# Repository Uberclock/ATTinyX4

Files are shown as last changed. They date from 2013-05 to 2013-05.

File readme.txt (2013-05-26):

NancyHacker is based on Logxen's ATTinyX4 breakout and is designed to allow easy reconfiguration of a NancyDriver.

Basic Operation:

1) Plug a NancyDriver into the NancyHacker and use a MicroUSB cable to supply power to the NancyHacker.

2) The LED on the NancyHacker will flash to read out the set current on the driver board in amps. First it will count out slow flashes (1 second on, 1 second off) representing the integer then short flashes (0.5 second on, 0.5 second off) representing the tenths. So, a brand new NancyDriver should arrive set to 1.2A and so should read one long flash followed by two short flashes and a pause.

3) The UP and DOWN buttons can be used to adjust the set current by tenths. The NancyHacker will then read out the new setting over the LED. That's all there is to it. :)

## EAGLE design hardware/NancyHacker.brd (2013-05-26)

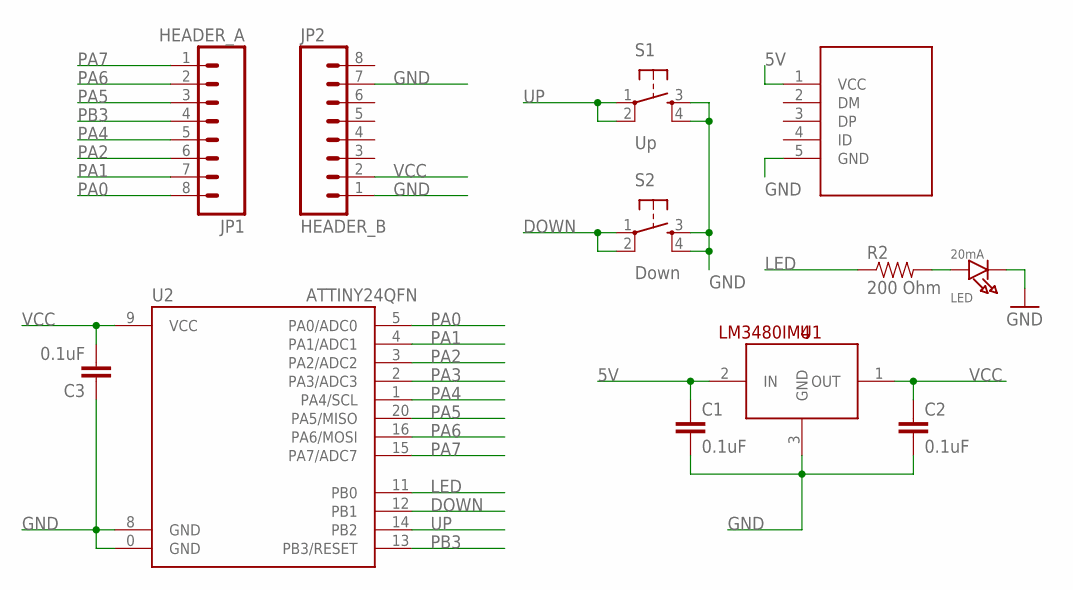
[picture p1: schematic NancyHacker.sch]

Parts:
C1, C2, C3: 0.1uF; 0603-CAP
JP1: HEADER_A; 1X08
JP2: HEADER_B; 1X08
LED: 20mA; CHIPLED_0603_NOOUTLINE
R2: 200 Ohm; 0402-RES
S1: Up; TACTILE_SWITCH_SMD
S2: Down; TACTILE_SWITCH_SMD
U1: LM3480IM4; SOT23-3
U2: ATTINY24QFN; QFN20
U$1: USB-MICROB-SMDRECEPT; USB-MICROB-RECEPT

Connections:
5V: C1.1, U1.2 (IN), U$1.1 (VCC)
DOWN: S2.1, S2.2, U2.12 (PB1)
GND: C1.2, C2.2, C3.1, JP2.1, JP2.7, LED.C, S1.3, S1.4, S2.3, S2.4, U1.3 (GND), U2.0 (GND), U2.8 (GND), U$1.5 (GND)
LED: R2.1, U2.11 (PB0)
PA0: JP1.8, U2.5 (PA0/ADC0)
PA1: JP1.7, U2.4 (PA1/ADC1)
PA2: JP1.6, U2.3 (PA2/ADC2)
PA3: U2.2 (PA3/ADC3)
PA4: JP1.5, U2.1 (PA4/SCL)
PA5: JP1.3, U2.20 (PA5/MISO)
PA6: JP1.2, U2.16 (PA6/MOSI)
PA7: JP1.1, U2.15 (PA7/ADC7)
PB3: JP1.4, U2.13 (PB3/RESET)
STATUS_LED_RESISTOR: LED.A, R2.2
UP: S1.1, S1.2, U2.14 (PB2)
VCC: C2.1, C3.2, JP2.2, U1.1 (OUT), U2.9 (VCC)

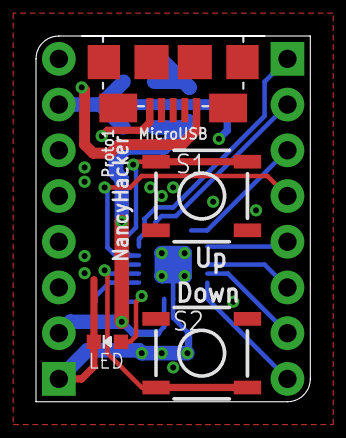
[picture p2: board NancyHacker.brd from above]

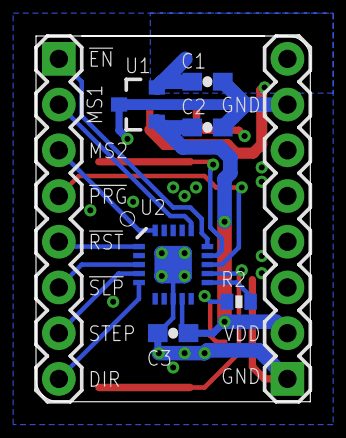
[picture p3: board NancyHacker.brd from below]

Board: 2 copper layers, 15.2 x 20.3 mm, 12 parts (8 on the bottom side), 15 nets.

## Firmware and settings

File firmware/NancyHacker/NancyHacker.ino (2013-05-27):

#include <Arduino.h>

#include "nancylib.h"

#define I2C_ADD    0xC0

#define LED_PIN    8
#define UP_PIN     10
#define DOWN_PIN   9

#define EN_PIN     7
#define MS1_PIN    6
#define MS2_PIN    5
#define RST_PIN    3
#define SLP_PIN    2
#define STEP_PIN   1
#define DIR_PIN    0


void setup() {
  pinMode(LED_PIN, OUTPUT);
  digitalWrite(LED_PIN, LOW);
  pinMode(UP_PIN, INPUT);
  digitalWrite(UP_PIN, HIGH);
  pinMode(DOWN_PIN, INPUT);
  digitalWrite(DOWN_PIN, HIGH);
  pinMode(EN_PIN, OUTPUT);
  digitalWrite(EN_PIN, HIGH);
  pinMode(MS1_PIN, OUTPUT);
  digitalWrite(MS1_PIN, LOW);
  pinMode(MS2_PIN, OUTPUT);
  digitalWrite(MS2_PIN, LOW);
  pinMode(RST_PIN, OUTPUT);
  digitalWrite(RST_PIN, HIGH);
  pinMode(SLP_PIN, OUTPUT);
  digitalWrite(SLP_PIN, HIGH);
  pinMode(STEP_PIN, OUTPUT);
  digitalWrite(STEP_PIN, HIGH);
  pinMode(DIR_PIN, OUTPUT);
  digitalWrite(DIR_PIN, HIGH);
}

int current = -1;
int time = millis();
int longs = 0;
int shorts = 0;
boolean up_state;
boolean down_state;
int up_cnt;
int down_cnt;
void loop() {
  if(time > -1) {
  // check buttons
  boolean up_btn = digitalRead(UP_PIN);
  boolean down_btn = digitalRead(DOWN_PIN);
  if(up_btn == up_state) {
    up_cnt = 0;
  }
  else {
    up_cnt++;
    if(up_cnt > 50) {
      up_state = up_btn;
      up_cnt = 0;
      if(up_state) up_pushed();
    }
  }
  if(down_btn == down_state) {
    down_cnt = 0;
  }
  else {
    down_cnt++;
    if(down_cnt > 50) {
      down_state = down_btn;
      down_cnt = 0;
      if(down_state) down_pushed();
    }
  }
  }
  
  // read current setting
  int new_current;
  if(connection_test(STEP_PIN, DIR_PIN, I2C_ADD)) {
    new_current = driver_read(STEP_PIN, DIR_PIN, I2C_ADD);
  }
  else {
    new_current = -1;
  }
  if(new_current == -1){
    time = -1;
  }
  
  if(new_current != current && new_current > -1) {
    current = new_current;
    longs = 0;
    shorts = 0;
    int t = current;
    while(t >= 100) {
      t -= 100;
      longs++;
    }
    while(t >= 10) {
      t -= 10;
      shorts++;
    }
    time = millis();
  }

  // flash current setting
  if(time > -1) {
    flash_current();
  }
}

void up_pushed() {
  int data = current + 10;
  if(data > 250) data = 250;
  driver_write(STEP_PIN, DIR_PIN, I2C_ADD, data);
}

void down_pushed() {
  int data = current - 10;
  if(data < 0) data = 0;
  driver_write(STEP_PIN, DIR_PIN, I2C_ADD, data);
}

void flash_current() {
  int state = millis() - time;
  for (int i=0;i<longs;i++) {
    if(time < (2*i+1)*1000) {
      digitalWrite(LED_PIN, HIGH);
      return;
    }
    else if(time < (2*i+2)*1000) {
      digitalWrite(LED_PIN, LOW);
      return;
    }
  }
  int basetime = 2*longs*1000;
  for (int i=0;i<shorts;i++) {
    if(time < basetime+(2*i+1)*500) {
      digitalWrite(LED_PIN, HIGH);
      return;
    }
    else if(time < basetime+(2*i+2)*500) {
      digitalWrite(LED_PIN, LOW);
      return;
    }
  }
  basetime += 2*shorts*500 + 1000;
  if(time > basetime) time = millis();
}

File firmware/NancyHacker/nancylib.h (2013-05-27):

#define I2C_READ   0x01
#define I2C_WRITE  0x00

void i2c_bangbyte(int scl, int sda, byte c) {
  for(int i=7;i>=0;i--) {
    // i2c data write
    digitalWrite(scl, LOW);
    delayMicroseconds(5);
    digitalWrite(sda, (c >> i) & 1);
    delayMicroseconds(5);
    digitalWrite(scl, HIGH);
    delayMicroseconds(10);
  }
}

byte i2c_readbyte(int scl, int sda) {
  byte c = 0;
  pinMode(sda, INPUT);
  digitalWrite(sda, HIGH);
  
  for(int i=7;i>=0;i--) {
    // i2c data read
    digitalWrite(scl, LOW);
    delayMicroseconds(10);
    digitalWrite(scl, HIGH);
    delayMicroseconds(5);
    c &= (digitalRead(sda) << i);
    delayMicroseconds(5);
  }
  
  pinMode(sda, OUTPUT);
}

void i2c_start(int scl, int sda) {
  // i2c setup
  pinMode(sda, OUTPUT);
  digitalWrite(sda, HIGH);
  pinMode(scl, OUTPUT);
  digitalWrite(scl, HIGH);
  delayMicroseconds(10);
  
  // i2c start
  digitalWrite(sda, LOW);
  delayMicroseconds(10);
}

boolean i2c_ack(int scl, int sda) {
  boolean res;
  // i2c ack
  digitalWrite(scl, LOW);
  delayMicroseconds(5);
  pinMode(sda, INPUT);
  digitalWrite(sda, HIGH);
  delayMicroseconds(5);
  digitalWrite(scl, HIGH);
  delayMicroseconds(5);
  res = digitalRead(sda);
  delayMicroseconds(5);
  pinMode(sda, OUTPUT);
  return res;
}

void i2c_repeatedstart(int sda, int scl) {
  // i2c repeated start
  digitalWrite(scl, LOW);
  delayMicroseconds(5);
  digitalWrite(sda, HIGH);
  delayMicroseconds(5);
  digitalWrite(scl, HIGH);
  delayMicroseconds(5);
  digitalWrite(sda, LOW);
  delayMicroseconds(5);
}

void i2c_stop(int sda, int scl) {
  // i2c stop
  digitalWrite(scl, LOW);
  delayMicroseconds(5);
  digitalWrite(sda, LOW);
  delayMicroseconds(5);
  digitalWrite(scl, HIGH);
  delayMicroseconds(5);
  digitalWrite(sda, HIGH);
  delayMicroseconds(5);
}

boolean connection_test(int scl, int sda, int add) {
  i2c_start(scl, sda);
  i2c_bangbyte(scl, sda, add & I2C_READ);
  boolean res = i2c_ack(scl, sda);
  i2c_stop(scl, sda);
  
  return res;
}

int driver_read(int scl, int sda, int add) {
  i2c_start(scl, sda);
  i2c_bangbyte(scl, sda, add & I2C_READ);
  i2c_ack(scl, sda);
  byte config = i2c_readbyte(scl, sda);
  i2c_ack(scl, sda);
  byte data = i2c_readbyte(scl, sda);
  boolean ack = i2c_ack(scl, sda);
  i2c_stop(scl, sda);
  
  if(ack)
    return data;
  else
    return -1;
}

void driver_write(int scl, int sda, int add, byte current) {
  i2c_start(scl, sda);
  i2c_bangbyte(scl, sda, add & I2C_WRITE);
  i2c_ack(scl, sda);
  i2c_bangbyte(scl, sda, 0x78);
  i2c_ack(scl, sda);
  i2c_bangbyte(scl, sda, current);
  i2c_ack(scl, sda);
  i2c_bangbyte(scl, sda, 0x00);
  i2c_ack(scl, sda);
  i2c_stop(scl, sda);
}

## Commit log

2013-05-26 Renamed sch and brd files
    [NancyHacker.brd, NancyHacker.sch]
2013-05-26 Initial commit of forked NancyHacker (Prototype 1)
    [NancyHacker.brd, NancyHacker.sch]
2013-05-26 Added BoM
2013-05-26 Moved pcb files into hardware directory
    [NancyHacker.brd, NancyHacker.sch]
2013-05-27 Initial firmware implementation
    still waiting on prototype NancyDriver and NancyHacker pcbs so code has
    not been tested

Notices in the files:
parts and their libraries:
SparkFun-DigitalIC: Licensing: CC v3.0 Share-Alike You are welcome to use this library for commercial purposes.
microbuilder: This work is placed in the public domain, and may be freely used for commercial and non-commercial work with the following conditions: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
